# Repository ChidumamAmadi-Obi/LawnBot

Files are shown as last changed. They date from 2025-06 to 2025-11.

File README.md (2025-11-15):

# LawnBot (under construction)

This repository documents the development of a **Wi-Fi-controlled lawn mowing robot** built around a **Raspberry Pi Pico 2 W**. The system uses the Pico's dual-core processor to efficiently handle real-time sensor data, motor control, and network communication concurrently.

The project combines **custom hardware (PCB design)**, **embedded software in C/C++**, and a lightweight **web UI** for control and testing.

## Preview 
Realtime WebSocket communication Demo

[](https://github.com/user-attachments/assets/c1d89f53-037a-400e-aac7-5eb62932627b)



## Current Features 
- Wi-Fi connectivity established through Pico 2 W  
- WebSocket communication pipeline between Pico and browser
- Basic motor control via DrRobot driver
- Obtacle detection with ToF sensors
- Test web interface for manual control (arrows, toggles, etc.)

## Hardware
- **Raspberry pi pico W2**
- **Custom PCB** (prototype + ongoing design)
- **Tof Sensor**
- **12V Motors with encoders** (planned)
- **DRI0044 DFrobot Dual motor driver**
- **12V Brushless DC motor with ESC**
- **Li-ion battery pack**

## How It Works

### Core 0: Communication and Control
 This core runs the main Arduino loop and handles all network and control tasks.
 1) On boot, core 0 **connects to Wifi and starts a web server** to serve te control interface *Webpage.h*, and initializes the WebSocket server.
 2) The *webSocketEvent()* function acts as the **main command parser** for incoming messages from the web UI.
 3) The *loop()* calls *handleMotorControl(motorSpeed, direction)*, which **translates the direction and speed into the correct PWM and digital signals for the motor driver**.
 4) Every second, the *loop()* calls *createJSON()*:
    * Locks Mutex to safely read the shared sensor data without risking corruption from Core 1.
    * Serializes the data into a JSON string.
    * **Broadcasts the JSON string to all connected web clients** via *webSocket.broadcastTXT()*.

 ### Core 1: Real-Time Sensor Reading
 This core is dedicated to reading sensors and calculating odometry with precise timing, independant of network latency.
 1) The core **initializes GPIO interrupts** on the encoder pins. Every change on these pins triggers an Interrupt Service Routine *(isrEncoder1(), isrEncoder2())*.
    * The **ISRs decode the quadrature signals** to determine the direction the motors are currently spinning. (happens in the background with minimal CPU usage).
2) In core 1's main loop, it **checks the ToF sensor every 100ms**, and if so:
   * Locks the Mutex and updates the shared *objectDistance* variable.
   * Sets the *objectDetectionWarning* flag if an object is closer than the *TOF_THRESHOLD*.
3) Every 250ms, *handleEncoders()* is called:
   * Temporarily disables interrupts to safely read and reser the *periodEncoderCount* variables.
   * **Calculates RPM of each motor**
   * Calls updateOdometry() to **calculate the total distance traveled by each wheel** using the *totalEncoderCount*.
```
RPM = (pulses_in_interval * 60) / (PULSES_PER_REVOLUTION * interval_in_seconds)
```



*Flowchart of code flow*

## PCB Development
first PCB was successfully designed, manufactured, and tested.
- Verified core functionality: Pico W2, motor driver, and power delivery
- Issues identified:
  * Missing decoupling capacitors led to noise and unwanted voltage spikes
  * No support for motor encoders
  * No ToF sensor integration
  * Lack of test points and indicator LEDs for debugging
- A redesigned PCB id currently in progress with fixes and explained functionality.
- Full details: PCB Design and Schematic README.md

## Setup Instructions 
1) Clone the repo:
```
git clone https://github.com/ChidumamAmadi-Obi/LawnBot.git
cd src/main
```
2) Open main.ino in ArduinoIDE with Raspberry Pi Pico board support (Raspberry Pi Pico/RP2040/RP2350 by Earle F. Philhower, III)
3) Make a new header file and name it *SSID.h*
4) In *SSID.h* copy these variables and fill out your wifi credentials:
```
const char* SSID = "YOUR_SSID";
const char* PASSWORD = "YOUR_PASSWORD";
```
5) Connect sensors and motors as per wiring diagram
```
  //PIN CONFIG
  constexpr uint8_t PWM2 = 0;
  constexpr uint8_t PWM1 = 1;
  constexpr uint8_t DIR2 = 2;
  constexpr uint8_t DIR1 = 3;
  constexpr uint8_t BDLC_PWM_PIN = 16;
  constexpr uint8_t WIFI_LED_PIN = 17;
```



7) Save this header file, and flash the code onto the Pico
8) Connect to the Pico's WiFi network and open the web interface for control

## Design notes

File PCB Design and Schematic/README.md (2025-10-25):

# PCB & Schematic Revision Notes
Current PCB validated the core functionality od the LawnBot, but after testing several areas for improvement became clear.

## Key Lessons from the first PCB
* Peripheral Oversight: Original design did not account for motor encoders and ToF sensors, both of which are critical for precise navigation and closed-loop control.
* Noise Management: Lack of proper decoupling capacitors resulted in electrical noise that impacted PCB performance.
* Debugging Limitations: Without test points, indicator LEDs, and clear labeling, diagnosing hardware/software integration issues took longer than it should have.

## Improvements in the Next Revision
* Encoder & ToF Integration for Automation: Dedicated connections for wheel encoders and distance sensors will be added for accurate motion control and autonomous driving.
* Noise Reduction: Strategic placement of decoupling capacitors and filtering components will stabilize power rails and improve overall reliability.
* Motor Driver Support: Circuit refinements to help the driver handle transients and reduce thermal stress. (Thicker tracks for higher currents, isolating motor driver from other more noise sensitive components).
* Debug-Friendly Design: Indicator LEDs for status monitoring, labeled headers, and test points for multimeter/oscilloscope probes.
* Better Documentation: A cleaner schematic and clearer silkscreen labeling to improve readability and handoff for other engineers.
    


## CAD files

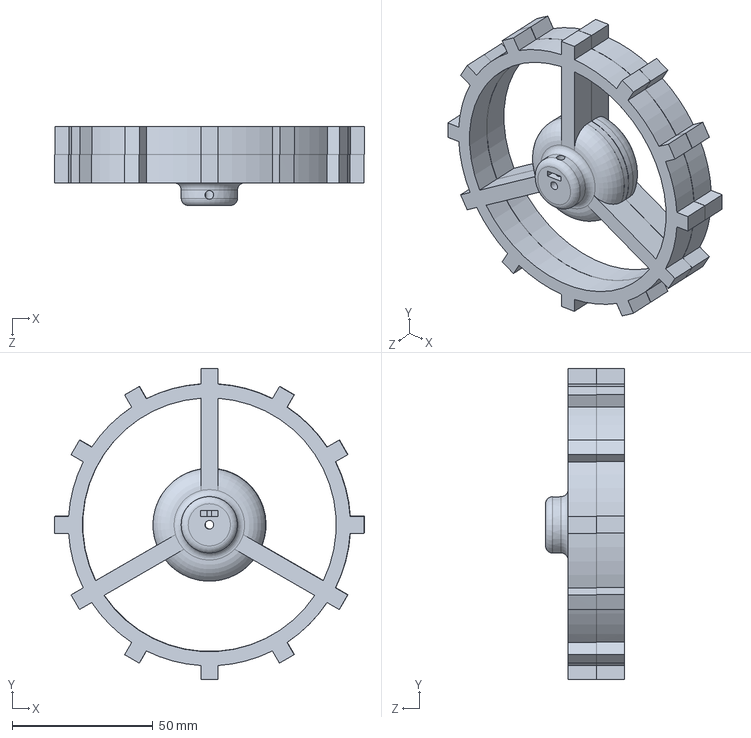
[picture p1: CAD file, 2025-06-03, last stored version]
Housing Design/WheelSW.SLDPRT
109.9 x 110.4 x 28.0 mm

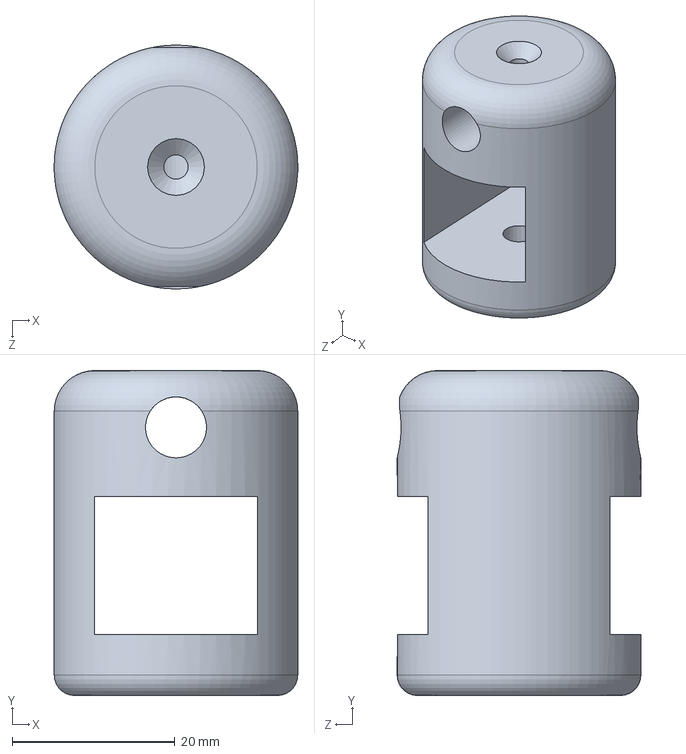
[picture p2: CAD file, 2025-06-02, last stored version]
Housing Design/blademountSW.SLDPRT
30.0 x 40.0 x 30.0 mm

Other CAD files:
Housing Design/WheelSTL.STL
Housing Design/blademountSW.STL

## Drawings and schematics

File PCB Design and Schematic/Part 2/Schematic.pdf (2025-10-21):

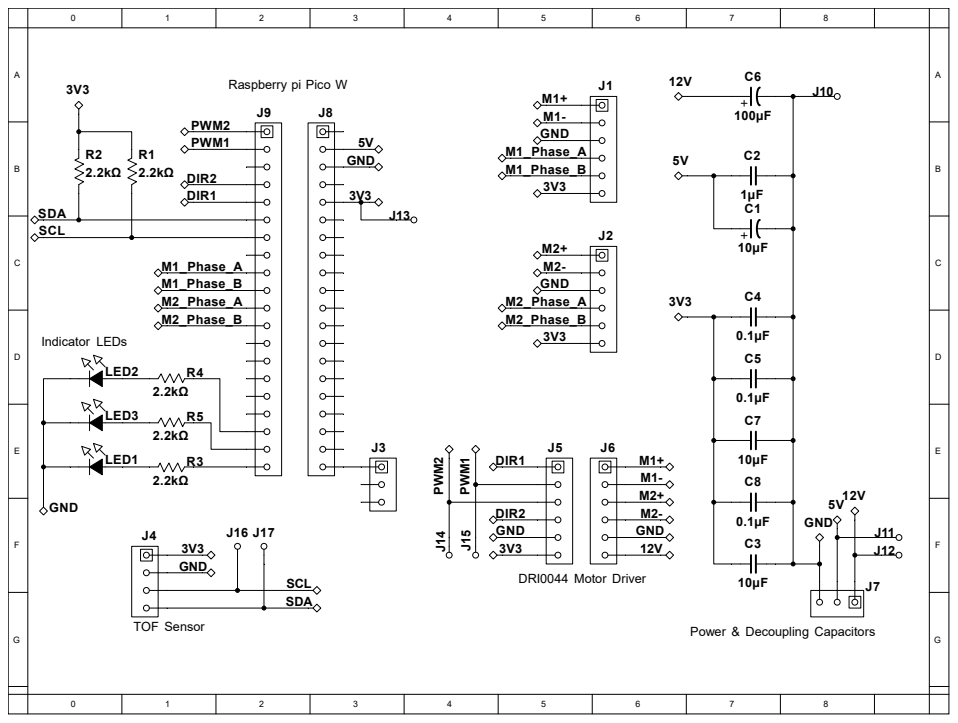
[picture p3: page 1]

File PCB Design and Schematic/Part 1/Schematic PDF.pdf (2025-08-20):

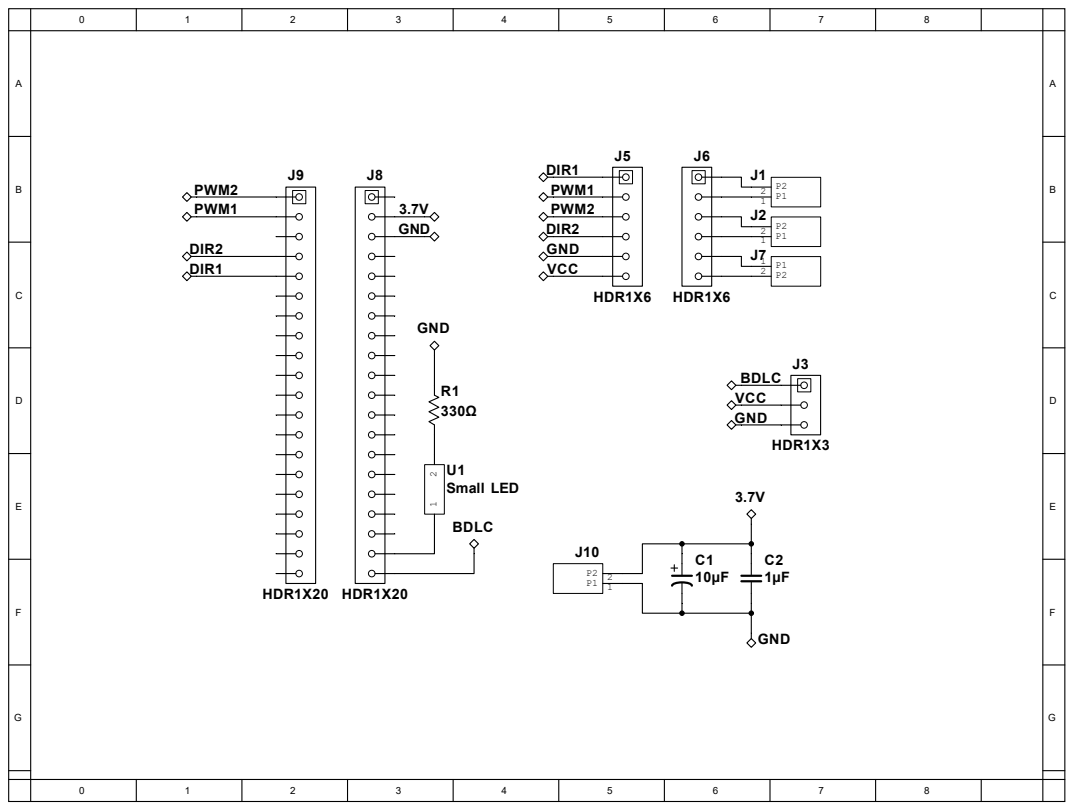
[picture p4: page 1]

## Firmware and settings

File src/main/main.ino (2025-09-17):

#include <Arduino.h>
#include <stdio.h>
#include <ArduinoJson.h>
#include <WiFi.h>
#include <WebServer.h>
#include <WebSocketsServer.h>
#include "Adafruit_VL53L0X.h"
#include "pico/mutex.h"
#include "pico/multicore.h"

#include "SSID.h"    // holds SSID information
#include "Config.h"
#include "WebPage.h"
#include "MotorControl.h"
#include "WifiManager.h"
#include "SensorReading.h"

unsigned long prevMillis = 0;

void core1_entry();

void setup() {
  Serial.begin(115200);
  mutex_init(&sensorMutex); // initialize mutex
  initTOFSensor();
  pinMode(Config::PWM1,OUTPUT);
  pinMode(Config::PWM2,OUTPUT);
  pinMode(Config::DIR1,OUTPUT);
  pinMode(Config::DIR2,OUTPUT);
  pinMode(Config::BDLC_PWM_PIN,OUTPUT);

  pinMode(Config::M1_PHASE_A,INPUT_PULLUP);
  pinMode(Config::M1_PHASE_B,INPUT_PULLUP);
  pinMode(Config::M2_PHASE_A,INPUT_PULLUP);
  pinMode(Config::M2_PHASE_B,INPUT_PULLUP);

  pinMode(Config::WIFI_LED_PIN,OUTPUT);

  multicore_reset_core1();
  multicore_launch_core1(core1_entry);

  analogWrite(Config::BDLC_PWM_PIN, 0); //makes sure the blade is not spinning  
  handleWifiConnection();
}
void loop() {
  currentMillis = millis();
  server.handleClient();
  webSocket.loop();

  json = createJSON();

  currentMillis = millis();
  if ( currentMillis - prevMillis >= Config::JSON_SENDING_INVERVAL) {
    webSocket.broadcastTXT(json);
    prevMillis = currentMillis;
  }
  webSocket.broadcastTXT(json);

  handleMotorControl(motorSpeed,direction);
}

void core1_entry() {
  initEncoders();
  while (true) {
    readTOFSensor();
    handleEncoders();
    delay(10);
  }
}

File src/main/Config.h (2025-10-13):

#ifndef CONFIG
#define CONFIG

#include <Arduino.h>
#include <WiFi.h>
#include <WebServer.h>
#include <WebSocketsServer.h>
#include "pico/mutex.h"
#include <stdio.h>

#define DEBUG_MODE 2

#if DEBUG_MODE == 0 // no debuging
#define DEBUG_WIFI_CONNECTION false
#define DEBUG_WEBSOCKET_COM false
#define DEBUG_MOTOR_CONTROL false
#define DEBUG_SENSOR_READINGS false
#endif
#if DEBUG_MODE == 1 // basic debugging
#define DEBUG_WIFI_CONNECTION true
#define DEBUG_WEBSOCKET_COM false
#define DEBUG_MOTOR_CONTROL false
#define DEBUG_SENSOR_READINGS false
#endif
#if DEBUG_MODE == 2 // wifi and websocket debugging
#define DEBUG_WIFI_CONNECTION true
#define DEBUG_WEBSOCKET_COM true
#define DEBUG_MOTOR_CONTROL false
#define DEBUG_SENSOR_READINGS false
#endif
#if DEBUG_MODE == 3 // sensor debugging
#define DEBUG_WIFI_CONNECTION true
#define DEBUG_WEBSOCKET_COM false
#define DEBUG_MOTOR_CONTROL true
#define DEBUG_SENSOR_READINGS true
#endif
#if DEBUG_MODE == 4 // throughouh debugging (not reccomended)
#define DEBUG_WIFI_CONNECTION true
#define DEBUG_WEBSOCKET_COM true
#define DEBUG_MOTOR_CONTROL true
#define DEBUG_SENSOR_READINGS true
#endif

void isrEncoder1();
void isrEncoder2();

namespace Config {

  //PIN CONFIG
  constexpr uint8_t PWM2 = 0;
  constexpr uint8_t PWM1 = 1;
  constexpr uint8_t DIR2 = 2;
  constexpr uint8_t DIR1 = 3;
  constexpr uint8_t BDLC_PWM_PIN = 16;
  constexpr uint8_t WIFI_LED_PIN = 17; 

  constexpr uint8_t M1_PHASE_A = 6;
  constexpr uint8_t M1_PHASE_B = 7;
  constexpr uint8_t M2_PHASE_A = 8;
  constexpr uint8_t M2_PHASE_B = 9;

  //WEBSOCKET
  constexpr uint16_t JSON_SENDING_INVERVAL = 1000;

  //SENSOR READING CONSTANTS
  constexpr uint16_t TOF_SCAN_INTERVAL = 100;
  constexpr uint8_t TOF_THRESHOLD = 50;
  constexpr uint16_t TOF_MAX = 8190;

  constexpr uint8_t RPM_MEASURE_INTERVAL = 250;
  constexpr uint8_t ENCODER_PPR = 11;              // pulses per rotation found in the datasheet
  constexpr uint8_t WHEEL_RADIUS = 3.5;            // cm radius
  constexpr uint8_t WHEEL_BASE = 10.20;            // cm between wheels

}

extern volatile unsigned long currentMillis;
extern unsigned long prevTOFScan;

extern uint8_t direction;
extern uint8_t motorSpeed;
extern bool cutting;
extern bool control; // manual
extern uint8_t state, temp;
extern volatile uint8_t objectDistance;
extern volatile bool objectDetectionWarning;

extern volatile uint16_t rpm1, rpm2;
extern volatile int coordX, coordY;
extern volatile float distanceLeft, distanceRight; // in meters

extern WebServer server;  
extern WebSocketsServer webSocket; 

extern String json;
extern String pastjson;
extern mutex_t sensorMutex;

#endif

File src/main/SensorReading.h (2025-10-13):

#ifndef SENSOR_READINGS
#define SENSOR_READINGS

#include "Config.h"

#if DEBUG_SENSOR_READINGS
#define debugSensors(x) Serial.print(x)
#define debugSensorsln(x) Serial.println(x)
#else 
#define debugSensors(x)
#define debugSensorsln(x)
#endif 

Adafruit_VL53L0X lox = Adafruit_VL53L0X();
extern unsigned long prevTOFScan;
unsigned long prevRPMMillis = 0;

volatile uint8_t prevState1 = 0,           prevState2 = 0;
volatile int32_t periodEncoderCount1 = 0,  periodEncoderCount2 = 0; // For RPM (reset every period)
volatile int32_t totalEncoderCount1 = 0,   totalEncoderCount2 = 0; 
volatile int32_t netCount1 = 0,            netCount2 = 0; 

//Tof Readings
void initTOFSensor() {
  if (!lox.begin()) {
    debugSensorsln(F("FAILED TO BOOT VL53L0X"));
    while(1);
  }
  debugSensorsln(F("VL53L0X SUCCESSFULLY CONNECTED\n\n"));
  lox.startRangeContinuous();
}
void readTOFSensor() {
  currentMillis = millis();
  if (currentMillis - prevTOFScan >= Config::TOF_SCAN_INTERVAL) {
    prevTOFScan = currentMillis;
    if (lox.isRangeComplete()) {

      mutex_enter_blocking(&sensorMutex); // protects shared variable
      objectDistance = lox.readRange();
      objectDetectionWarning = (objectDistance <= Config::TOF_THRESHOLD);
      mutex_exit(&sensorMutex);

      debugSensors("Distance in mm: ");
      if (objectDistance != 8190) {
        debugSensorsln(objectDistance);
      } else if (objectDistance <= 0) {
        // error
      }
    }
  }  
}

//Encoder Readings
void isrEncoder1() { // isrs get called every encoder pulse
  uint8_t state = (digitalRead(Config::M1_PHASE_B) << 1) | digitalRead(Config::M1_PHASE_A); 
  switch ((prevState1 << 2) | state) {
    case 0b0001: case 0b0111: case 0b1110: case 0b1000:
      totalEncoderCount1++; periodEncoderCount1++; break; // Forward
    case 0b0010: case 0b1011: case 0b1101: case 0b0100:
      totalEncoderCount1--; periodEncoderCount1--; break; // Backward
  }
  prevState1 = state;
}
void isrEncoder2() {
  uint8_t state = (digitalRead(Config::M2_PHASE_B) << 1) | digitalRead(Config::M2_PHASE_A);
  switch ((prevState2 << 2) | state) {
    case 0b0001: case 0b0111: case 0b1110: case 0b1000:
      totalEncoderCount2++; periodEncoderCount2++; break; // Forward
    case 0b0010: case 0b1011: case 0b1101: case 0b0100:
      totalEncoderCount2--; periodEncoderCount2--; break; // Backward
  }
  prevState2 = state;
}
void initEncoders() {
  prevState1 = (digitalRead(Config::M1_PHASE_B) << 1) | digitalRead(Config::M1_PHASE_A);
  prevState2 = (digitalRead(Config::M2_PHASE_B) << 1) | digitalRead(Config::M2_PHASE_A);
  
  attachInterrupt(digitalPinToInterrupt(Config::M1_PHASE_A), isrEncoder1, CHANGE);
  attachInterrupt(digitalPinToInterrupt(Config::M1_PHASE_B), isrEncoder1, CHANGE);
  attachInterrupt(digitalPinToInterrupt(Config::M2_PHASE_A), isrEncoder2, CHANGE);
  attachInterrupt(digitalPinToInterrupt(Config::M2_PHASE_B), isrEncoder2, CHANGE);
}

void handleEncoders() {
  currentMillis = millis();
  if ( currentMillis - prevRPMMillis >= Config::RPM_MEASURE_INTERVAL) {
    noInterrupts();                        // Disable interrupts
    int32_t count1 = periodEncoderCount1;
    int32_t count2 = periodEncoderCount2;
    periodEncoderCount1 = 0;
    periodEncoderCount2 = 0;
    Interrupts();                         // Re-enable interrupts
    // disableing and enabling interrupts makes sure instructions execute
    // completely without being interrupted by the ISR


    mutex_enter_blocking(&sensorMutex);
    rpm1 = abs(count1) * 60 / (Config::ENCODER_PPR * (Config::RPM_MEASURE_INTERVAL / 1000.0)); // Calculate RPM (absolute value for speed display)
    rpm2 = abs(count2) * 60 / (Config::ENCODER_PPR * (Config::RPM_MEASURE_INTERVAL / 1000.0));
    mutex_exit(&sensorMutex);

    prevRPMMillis = currentMillis;
  }
}

#endif

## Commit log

2025-06-02 Designed holding for weed wackers
    [blademountSW.SLDPRT, blademountSW.STL]
2025-06-03 Added wheels fit for n20 motor
    [WheelSTL.STL, WheelSW.SLDPRT]
2025-08-29 Updated motor control function
2025-09-13 Added pin Configuration
2025-09-17 stream current rpm to webpage
2025-10-10 updated to use power distrobution board
2025-10-10 Updated schematic
2025-10-13 volatile + disabling + enabling interrupts for ISR
2025-10-25 Designed PCB and exported Gerber files
